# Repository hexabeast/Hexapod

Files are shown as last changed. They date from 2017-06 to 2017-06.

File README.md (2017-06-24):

WARNING : If you want to reproduce it, the guide is not 100% complete, you'll need to figure out how to achieve some parts of the creation on your own.

Things needed to build the robot:

- A 3D Printer
- 2 LEGO Technic Steel Ball Caster
- 21 servos (standard size, like the MG996R on Amazon)
- A Raspberry Pi 2
- A Breadboard and wires
- 18650 battery cases and li-ion batteries (2x3.7V)
- Any slim portable smartphone battery (for the Pi)

To build the robot, refer to the schematic picture "robot.png" in this repository. 
You'll need additional materials (tape, glue...) to assemble the robot.

The slim portable smartphone battery should supply power directly to the Pi, and the li-ion batteries are for the 21 servos. 
Use the breadboard to do that and add 2 interruptors (one for the Pi, one for the servos).

Each servo needs to be connected to a GPIO pin on the raspberry.
For each leg clockwise, starting from the back-left leg, and starting from the motor at the extremity of the legs, here is are the GPIO numbers on which the servos should be connected:

4
17
27

22
5
11

13
19
26

18
23
24

25
8
12

16
20
21

wheel servos:
7
2

camera servo:
15

You also need to install pi-blaster ( https://github.com/sarfata/pi-blaster ), flask for Python 3, and ffmpeg on the Raspberry Pi, and put the content of the "code" folder in your home directory. 
Configure the Pi to run "sudo python3 script.py" on boot.
Configure the Pi to connect to your wifi network, or generate its own network.
Then, connect to your_pi_local_ip_adress:8000 on any browser on any device connected to the same network as the Pi, and you should be able ton control the robot.

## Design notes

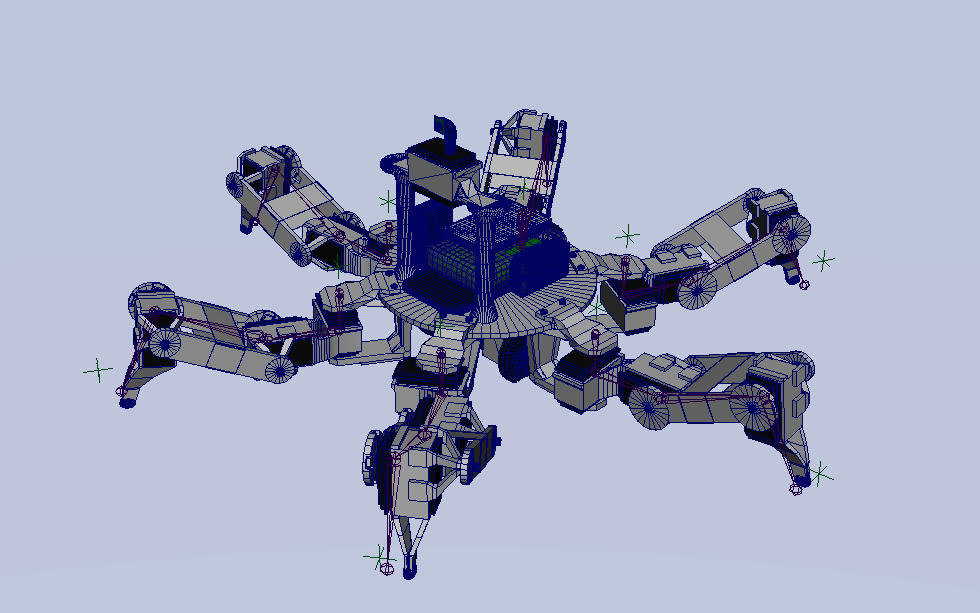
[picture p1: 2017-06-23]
robot.png

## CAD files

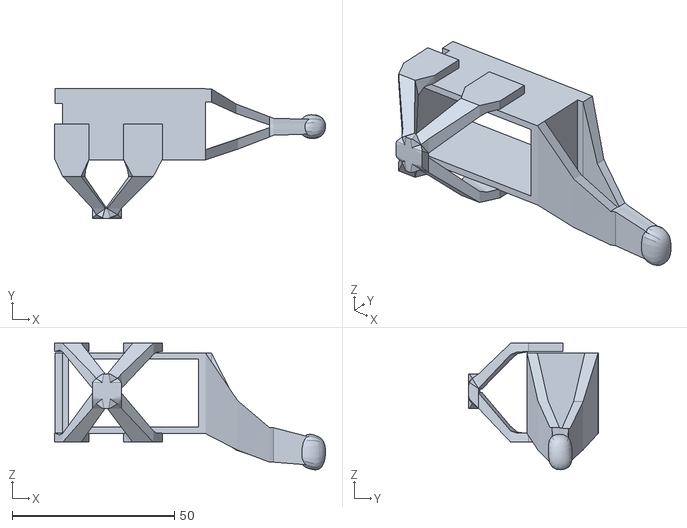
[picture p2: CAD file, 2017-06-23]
Patte_bout.stl
83.6 x 40.0 x 39.0

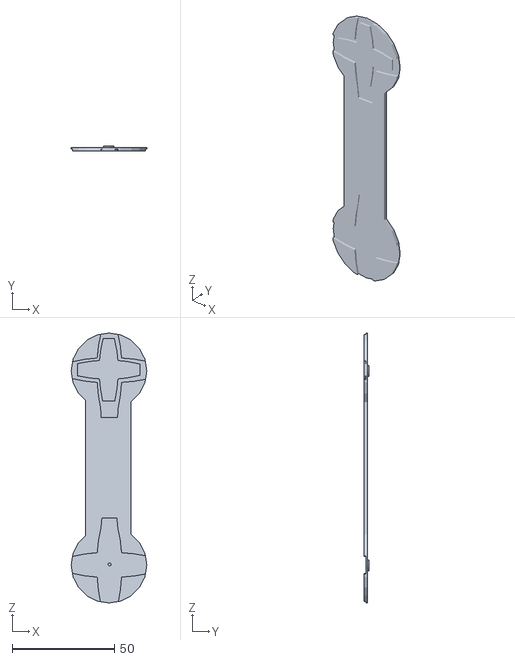
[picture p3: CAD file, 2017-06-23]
Patte_pont.stl
37.1 x 2.54 x 132.4

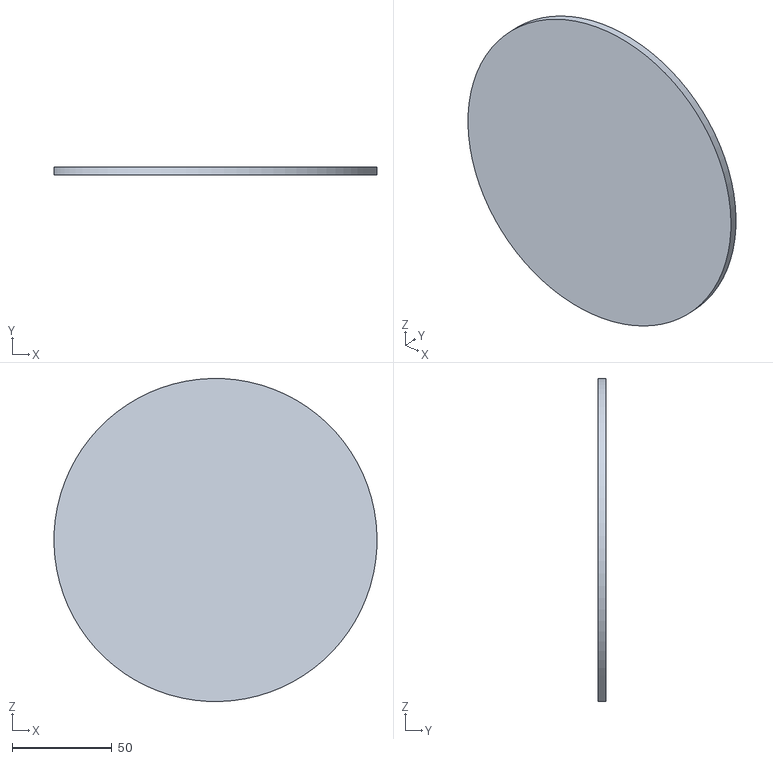
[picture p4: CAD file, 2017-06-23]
Base.stl
161.9 x 4.03 x 161.9

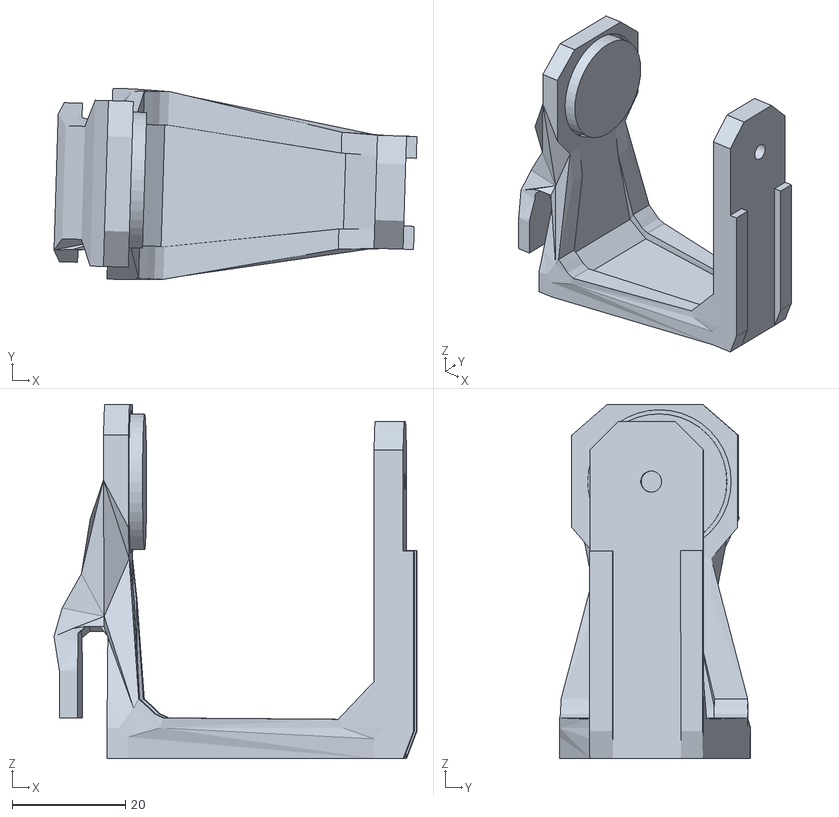
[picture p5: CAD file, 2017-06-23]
Patte_link1.stl
64.2 x 33.8 x 62.7

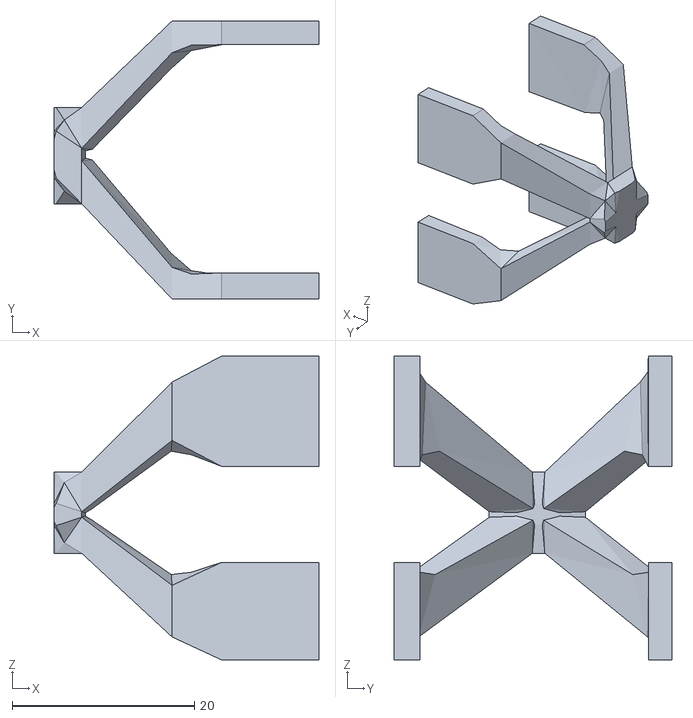
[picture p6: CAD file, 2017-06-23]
Patte_pontext.stl
29.0 x 30.5 x 33.3

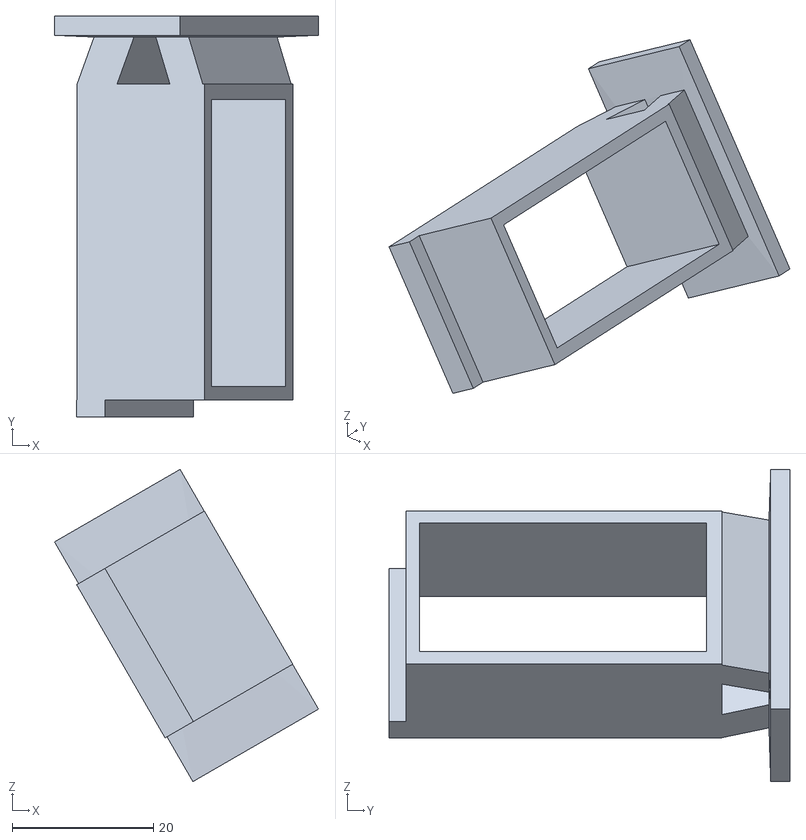
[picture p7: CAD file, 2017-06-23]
support_roue.stl
37.3 x 56.7 x 44.2

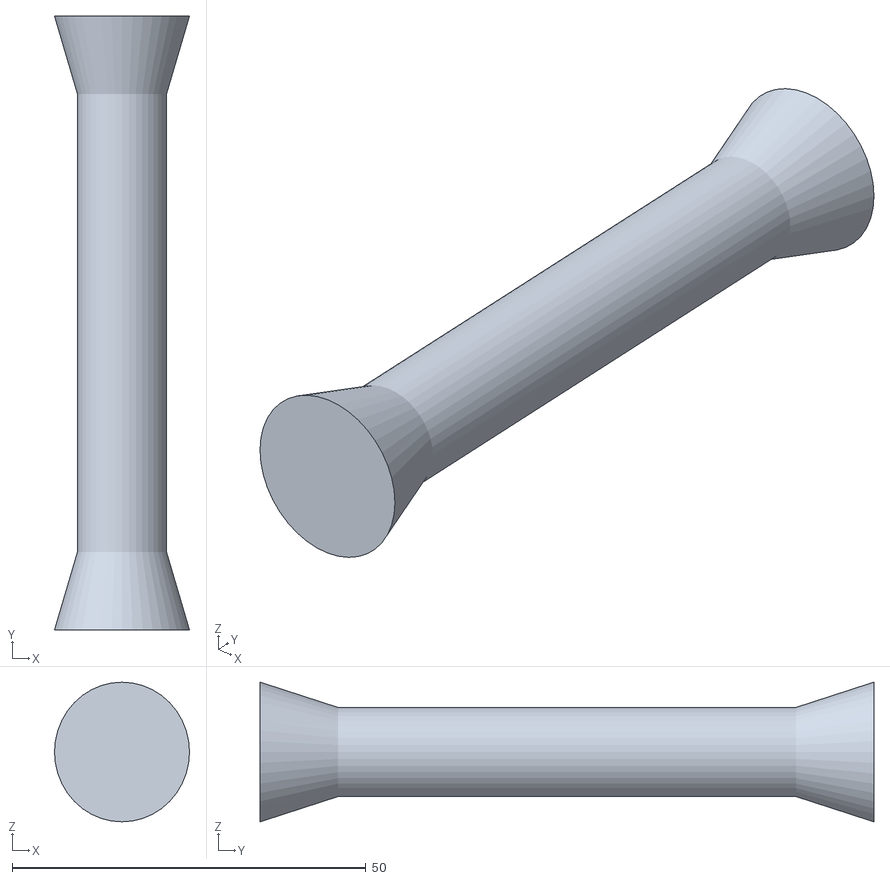
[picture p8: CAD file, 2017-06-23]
pilier.stl
19.1 x 86.7 x 19.7

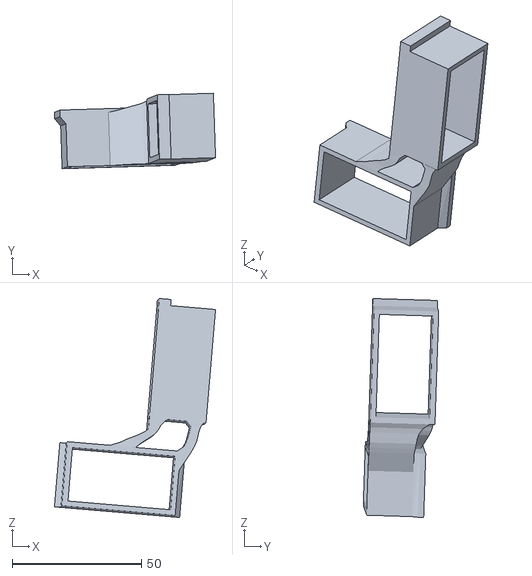
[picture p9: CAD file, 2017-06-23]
Patte_link2.stl
62.4 x 29.3 x 84.8

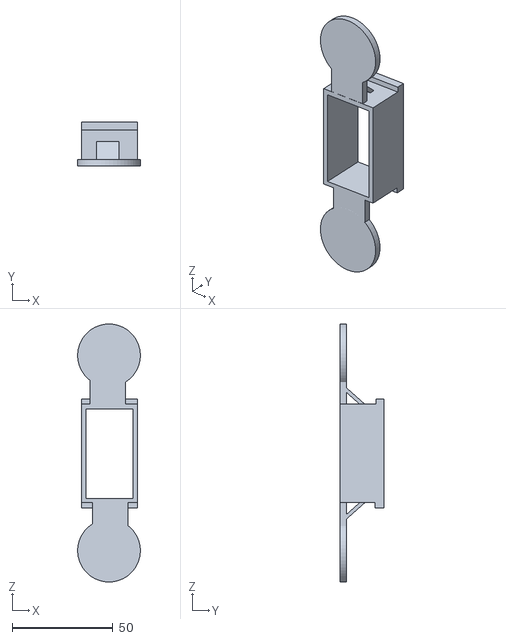
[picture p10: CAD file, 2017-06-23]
support_camera.stl
31.0 x 22.0 x 127.9

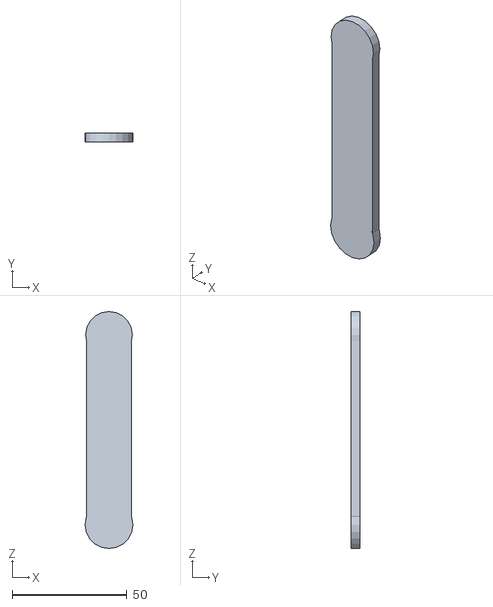
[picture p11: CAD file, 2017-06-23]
Patte_pont2.stl
20.9 x 4.00 x 103.3

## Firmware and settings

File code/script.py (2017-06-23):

#import RPi.GPIO as GPIO
import time
from tkinter import *
import os
from subprocess import Popen
from subprocess import PIPE
import threading
import sys,tty,termios
import socket
from flask import Flask, render_template, request, redirect, url_for, make_response
from multiprocessing import Process
from random import random

fd = sys.stdin.fileno()
oldtermios=termios.tcgetattr(fd)

#GPIO.setmode(GPIO.BOARD)

fini = False
direction = 0
origin = (0.53,0.33,0.54)
campos = 0.48

roues = [7,2]
camid = 15

ipattes = [[0 for i in range(3)] for j in range(6)]
pattes = [[0 for i in range(3)] for j in range(6)]
opattes = [[0 for i in range(3)] for j in range(6)]

ipattes[0][0] = 4
ipattes[0][1] = 17
ipattes[0][2] = 27

ipattes[1][0] = 22
ipattes[1][1] = 5
ipattes[1][2] = 11

ipattes[2][0] = 13
ipattes[2][1] = 19
ipattes[2][2] = 26


ipattes[3][0] = 18
ipattes[3][1] = 23
ipattes[3][2] = 24

ipattes[4][0] = 25
ipattes[4][1] = 8
ipattes[4][2] = 12

ipattes[5][0] = 16
ipattes[5][1] = 20
ipattes[5][2] = 21


#frequencyhertz = 50
#mspercycle = 1000/frequencyhertz

st = " --gpio "
for i in range(6):
    for j in range(3):
        #GPIO.setup(ipattes[i][j],GPIO.OUT)
        if i == 0 and j == 0:
            st+=str(ipattes[i][j])
        else:
            st+=","+str(ipattes[i][j])
        #pattes[i][j] = GPIO.PWM(ipattes[i][j],frequencyhertz)

        #pattes[i][j].start(30+j*10)
st+=","+str(roues[0])
st+=","+str(roues[1])
st+=","+str(camid)
os.system("sudo /etc/pi-blaster-master/pi-blaster"+st)

movelist = []


def movet(i,j,pos):
    global movelist
    movelist.append((i,j,pos))

def disablecam():
    st = 'sudo echo "'+str(camid)+'='+str(0)+'">/dev/pi-blaster'
    #Popen(st,shell=True,stdin=None,stdout=None,stderr=None,close_fds=True)
    
def disableroues():
    st = 'sudo echo "'+str(roues[0])+'='+str(0)+'">/dev/pi-blaster'
    st+= ' && '+ 'sudo echo "'+str(roues[1])+'='+str(0)+'">/dev/pi-blaster'
    Popen(st,shell=True,stdin=None,stdout=None,stderr=None,close_fds=True)

def movecam(f):
    global campos
    if campos+f<0.95 and campos+f>0.14:
        campos = campos+f
    
    pos = min(0.9,campos)
    if pos != 0:
        pos = pos*0.12
        pos+=0.01
    st = 'sudo echo "'+str(camid)+'='+str(pos)+'">/dev/pi-blaster'

    Popen(st,shell=True,stdin=None,stdout=None,stderr=None,close_fds=True)

def moveroues(a,b):
    b = 1-b
    a+=0.04
    b+=0.04

    a = a*0.12
    a+=0.01

    b = b*0.12
    b+=0.01
    
    st = 'sudo echo "'+str(roues[0])+'='+str(a)+'">/dev/pi-blaster'+" && "+'sudo echo "'+str(roues[1])+'='+str(b)+'">/dev/pi-blaster'
    Popen(st,shell=True,stdin=None,stdout=None,stderr=None,close_fds=True)

def moveg(i,j,pos):
    global movelist, opattes
    opattes[i][j] = (pos,100)
    movelist.append((i,j,pos))

def moveh(i,j,pos,speed):
    global opattes
    opattes[i][j] = (pos,speed)

def applymove():
    global movelist, pattes
    if len(movelist)>0:
        args = []
        k = 0
        for ele in movelist:
            k+=1
            i,j,pos = ele
            pattes[i][j] = pos
            if pos != 0:
                pos = pos*0.12
                pos+=0.01
            args.append('sudo echo "'+str(ipattes[i][j])+'='+str(pos)+'">/dev/pi-blaster')
            if k < len(movelist):
                args.append(" & ")
        Popen("".join(args),shell=True,stdin=None,stdout=None,stderr=None,close_fds=True)
    movelist = []
    
def move(i,j,pos):
    global opattes, pattes
    opattes[i][j] = (pos,100)
    pattes[i][j] = pos
    if pos != 0:
        pos = pos*0.12
        pos+=0.01
    st = 'sudo echo "'+str(ipattes[i][j])+'='+str(pos)+'">/dev/pi-blaster'

    Popen(st,shell=True,stdin=None,stdout=None,stderr=None,close_fds=True)
    #print('sudo echo "'+str(ipattes[i][j])+'='+str(pos)+'">/dev/pi-blaster')


def moveorigin():
    for i in range(6):
        for j in range(3):
            pass
            moveg(i,j,origin[j])
    disableroues()
    applymove()
    time.sleep(0.4)
    
moveorigin()
movecam(0)




app = Flask(__name__)
@app.route('/')
def index():
    return render_template('index.html')







def shutserver():
    global app
    func = request.environ.get('werkzeug.server.shutdown')
    if func is None:
        print("FLASKERROR")
    func()
    
def setfini():
    global fini,fd,oldtermios
    fini = True
    for i in range(6):
        for j in range(3):
            move(i,j,0)

    disablecam()
    time.sleep(0.5)
    termios.tcsetattr(fd,termios.TCSADRAIN,oldtermios)
    print("OK")
    sys.exit()
    
def getfini():
    global fini
    return fini


def shut():
    setfini()
    shutserver()
    return "Shutdown..."

@app.route('/<changepin>', methods=['POST'])
def reroute(changepin):

    changePin = int(changepin) #cast changepin to an int

    if changePin == 1:
        setdir(3)
    elif changePin == 2:
        setdir(4)
    elif changePin == 3:
        setdir(5)
    elif changePin == 4:
        setdir(6)
    elif changePin == 5:
        setdir(1)
    elif changePin == 6:
        setdir(2)
    elif changePin == 7:
        movecam(-0.15)
    elif changePin == 8:
        movecam(0.15)
    elif changePin == 0:
        setdir(0)
    elif changePin == 10:
        shut()
    elif changePin == 11:
        setdir(10)
    elif changePin == 12:
        setdir(9)
    elif changePin == 13:
        setdir(7)
    elif changePin == 14:
        setdir(8)
    elif changePin == 15:
        setdir(11)
    elif changePin == 16:
        setdir(12)
    elif changePin == 17:
        setdir(13)
    elif changePin == 18:
        setdir(-3)
    elif changePin == 19:
        setdir(-4)
    elif changePin == 20:
        setdir(14)
    elif changePin == 21:
        setdir(15)
    elif changePin == 22:
        setdir(16)    

    response = make_response(redirect(url_for('index')))
    return(response)


sltime = 0.3

decay = 0

def setdecay(x):
    global decay
    decay = float(x)/100
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
